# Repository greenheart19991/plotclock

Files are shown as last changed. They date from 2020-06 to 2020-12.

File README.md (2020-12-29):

# Plotclock

A robotic clock that writes current time with a marker.  

The way it functions is simple: the robot draws the time
on every new minute. At the beginning of a minute previously
drawn time becomes erased and new one appears on the board
again.

<p align="center">
  
</p>

## Demo

<p align="center">
  
</p>

## Table of Contents

* [Prerequisites](#prerequisites)
    - [Software](#software)
    - [Hardware & Supplies](#hardware--supplies)
* [Getting Components Ready](#getting-components-ready)
* [Assembling](#assembling)
    - [Mechanics](#mechanics)
    - [Electronics](#electronics)
        + [Prepare RTC Module](#prepare-rtc-module)
        + [Setup Voltage Regulator](#setup-voltage-regulator)
        + [Wiring Diagram](#wiring-diagram)
    - [Assembled Project](#assembled-project)
* [Firmware](#firmware)
    - [Installation](#installation)
    - [Calibration](#calibration)
* [Operating Details](#operating-details)
    - [Positioning To Specific Point](#positioning-to-specific-point)
    - [Drawing Chars](#drawing-chars)
    - [Boundaries](#boundaries)
* [Customization](#customization)
* [Known Issues](#known-issues)
* [Acknowledgments](#acknowledgments)

## Prerequisites

### Software

* Arduino IDE;
* KOMPAS-3D v18 in case you want to customize components.

### Hardware & Supplies

* Arduino UNO (any Rev);
* SG90 servo motors - x3;
* LM2596S step-down voltage regulator;
* ChronoDot V2.0 real time clock module;
* 4.7k Ohm resistors - x2 (for ChronoDot module);
* CR2016 battery;
* 5.5 x 2.1mm DC Female to 2 Male power splitter cable;
* 5.5 x 2.1mm power jack socket;
* DC power supply 12V 2A;
* Whiteboard marker (dry-wipe);

##### Screws & Nuts

* M3 x 12mm pan head screws - x8; 
* M3 x 16mm pan head screws - x1;
* M2.5 x 16mm pan head screws - x7; 
* M3 nuts - x9;
* M2.5 nuts - x7;
* M3 washers - x7;
* M2.5 washers - x1;
* SG90 default screws;

##### Other

* Jumper wires;
* Some glue;
* Some screws and nuts to fix the circuits.

## Getting Components Ready

It is designed to print all of the robot components with 3d-printer.
But you are free to choose another way to produce them.

You can find 3d-models of components under **plotclock_details**
directory. There are both separate files for each component
and **all_in_one** file that contains all of them.
Both are exported to STL format and ready to print.

## Assembling

### Mechanics

Put components together according to pictures below.

<p align="center">
  
</p>

<p align="center">
  
</p>

<p align="center">
  
</p>

Before joining default servo levers to servos themselves
(on the pictures above they have already been joined), set
servo shafts in corresponding positions:
* servo bottom: all the way to the end of min angle;
* servo right: all the way to the end of min angle;
* servo left: all the way to the end of max angle.  

Next, without rotating shafts, attach servo levers to servos
exactly as on the pictures below. After that you can rotate servo
shafts as you want and join printed levers.

<p align="center">
  
</p>

<p align="center">
  
</p>

When joining levers using screws and nuts, glue nuts to
levers to prevent them from loosening.

<p align="center">
  
</p>

<p align="center">
  
</p>

<p align="center">
  
</p>

<p align="center">
  
</p>

<p align="center">
  
</p>

<p align="center">
  
</p>

<p align="center">
  
</p>

Glue a piece of either cloth or cotton to eraser.

<p align="center">
  
</p>

<p align="center">
  
</p>

### Electronics

#### Prepare RTC Module

1. Solder both of pin headers into ChronoDot v2.0 RTC module.
1. Solder both of resistors into the module.
1. Install CR2016 battery on the module.

<p align="center">
  
</p>

#### Setup Voltage Regulator

Put 12V into the LM2596S voltage regulator and adjust it down
to make an output voltage 5.5V.  

#### Wiring Diagram

Connect all the modules together according to the wiring diagram
below.

<p align="center">
  
</p>

To prevent PCBs from moving make something kind of platform or
box for them and fix PCBs on it with screws and nuts.

### Assembled Project

<p align="center">
  
</p>

## Firmware

Sketch and its dependencies are located under **plotclock_code**
directory.

### Installation

Copy all the libraries from **plotclock_code/libraries** directory
to your machine's Arduino libraries directory. Now you are
ready to compile and upload the sketch.

### Calibration 

To be sure marker is positioned correctly you should calibrate
servo values for some predefined positions. Set appropriate values
for the following macros in the sketch:
* `SERVO_LEFT_ANGLE_180` - left servo value when its lever
rotated 180 degrees and is parallel to the board;
* `SERVO_LEFT_ANGLE_90` - left servo value when its lever
rotated 90 degrees and is perpendicular to the board;
* `SERVO_RIGHT_ANGLE_0` - right servo value when its lever
rotated 0 degrees and is parallel to the board.

This lever positions are shown in pictures below.

<p align="center">
  
</p>

<p align="center">
  
</p>

To calibrate Z-axis marker positioning, change the following
macros of bottom servo values:
* `SERVO_BOTTOM_PV_WR_BOTTOM` - position of marker when it touches
the board and chars becomes written;
* `SERVO_BOTTOM_PV_WR_UP` - position of marker to move it between
chars without writing a line;
* `SERVO_BOTTOM_PV_ERS_BOTTOM` - marker is in the eraser;
* `SERVO_BOTTOM_PV_FULLUP` - marker is above the eraser. 

After calibrating and uploading the sketch the robot can be
considered fully assembled and good to go. Since RTC module contains
the battery you don't have to reupload the sketch whenever
you turn the power off to setup the actual time - the module
keeps track of it by itself.

## Operating Details

This section describes provided solution for drawing figures
and intended to help you to deal with sketch and customize
it if necessary.

### Positioning To Specific Point

To move marker to specific point of the drawing plane
you have to rotate servo shafts by specific angle.
In order to draw a char you have to perform a series
of movements to different points; for each of them
you have to know rotation angles for both servo left
and right shafts.

To provide an ability to move the marker by specifying
position of point but not the rotation angles,
virtual coordinate plane was defined. The origin of the
plane is located relative to the servo shafts axes,
and it's position is configurable.

Plane lines unit is millimeter. It thus allows you to
understand the physical location of particular point
without additional units conversion.

This coordinate plane is shown on picture below.
Blue, red and green colors indicate the corresponding
parts of the 'arms' lever system (top view) for one
of the possible marker positions. Point D here is a marker
position, and points A and B indicate servo shafts axes.
The AK distance is equal to the length of the AF lever.
Distances OL and LN are customizable and added to provide
ability to configure origin position.

<p align="center">
  
</p>

Since all of the valuable distances between points are known
and distances MD and DN can be calculated from provided x and y
coordinates, it is possible to calculate the angles FAB and ABG
that represent either angles of the servos or those from which
they can be obtained (servo left angle = FAB, servo right
angle = 180 - ABG).

Algorithm to find these values is implemented in `getServoAngles`
function. To move the marker use `moveTo` function. It uses
`getServoAngles` within itself.

### Drawing Chars

Since coordinate plane is defined, you can describe any figure
you want with a function. And, as soon as you define a
function, you can draw this figure by iterating over axis values,
passing these values to a function and thus getting the coordinates
of points that outline of figure consists of.

Exactly this way all chars becomes drawn. But, in order to simplify
functions, chars are described as a set of primitives.
These are lines, circles and ellipses.

For example, number '1' consists of 2 lines, while number '8' is
2 ellipses. Hence, to draw these numbers the robot sequentially
draw their primitives.

### Boundaries

Due to design features, not all of the board surface area is available
for drawing. For current design all the points that the robot can
positions is shown on picture below.

This area is indicated in red. The board is located according
to its actual location. Black rectangle indicates the max area
determined for drawing chars.

<p align="center">
  
</p>

Take this information into account if you want to customize
chars, positions or sizes, or if you going to draw your own figures.

## Customization

You can find editable models of the robot components under
**plotclock_details/kompas_models** directory. 

The project also provides a tool to show available drawing
area (described above) for a specific design setup. This
tool is located under **plotclock_design** directory and
can help you determine sizes or positions of different
components for new design and define drawing area boundaries.

## Known Issues

SG90 are pretty chip servos and cannot provide guaranteed
ability to rotate their shaft by an angle lower then
~0.75 degree under the marker weight. Therefore quite big
positioning errors occur. As a result there are jagged lines
and currently no ability of physically accurate positioning.

To solve it, more accurate and expensive servos should be
used to give an ability to rotate shafts by at least 0.1 degree.

## Acknowledgments

Thanks to [joo](https://www.thingiverse.com/joo/about)
from [Thingiverse](https://www.thingiverse.com/) for idea
and initial design of components. See original project
[here](https://www.thingiverse.com/thing:248009#Instructions).

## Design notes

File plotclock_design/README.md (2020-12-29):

# Plotclock Design

A tool to show available drawing area for a specific design setup
of the Plotclock.

It can be useful in case you are customizing existing components
or creating your own design. It can help you determine sizes of
these components as well as their positions and drawing area
boundaries.

## Usage

To start the tool open index.html in browser. You'll see
all the points to that marker can be positioned for currently
set robot design.

To edit components settings, edit corresponding constants in
*plotclock.js* file and refresh the page to update the area.

In case available drawing area for some reason was not be rendered
check your design setup and see occurred errors in browser console.

### Component Settings

All the constants are named according to points and segments
described in 'Operating Details' section of main README.
Take a look on the figure provided in this section to determine
constant components.

### Display Settings

You can also change some display behaviour. Main setting here
is `pxInUn` that specifies number of display pixels per
coordinate plane unit. The larger value you set, the larger image
will be, and the higher resolution you will have. You can find this
setting under `show points on page` section in code. 

### Overlay Components 

The tool also provides a Photoshop mockup that can simplify
you putting the board outline and eraser on created image
and determining the chars drawing area. You can find this
mockup as well as example result of tool usage
(for current design setup) under **coverage_maps** directory. 

## Known Issues

Due to representation of numbers in computer, calculation
errors take place. Thus for some **correct** design settings
an error can be thrown and coverage map will not be rendered.
In such situation in console you'll see an error like this:

<p align="center">
  
</p>

Currently, to work around this issue you should change
your design settings a little bit, e.g. for one tenth of mm.

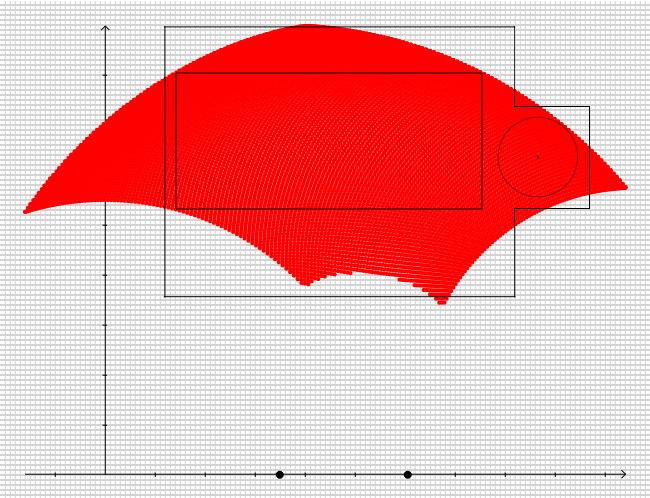
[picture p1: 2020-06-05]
plotclock_design/coverage_maps/coverage_map_x1.png

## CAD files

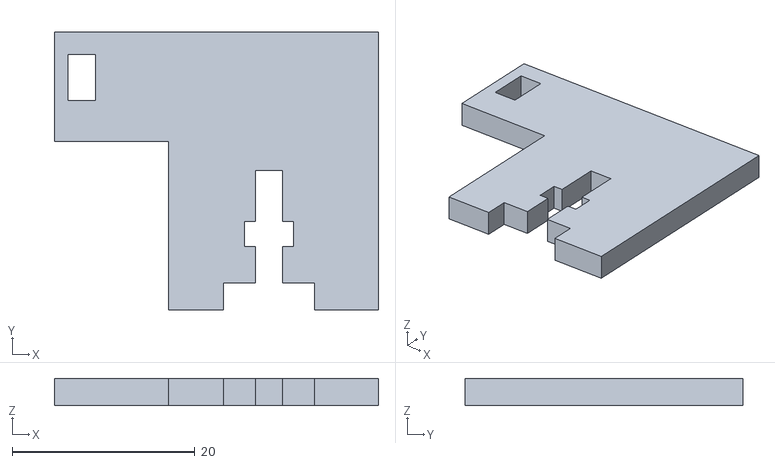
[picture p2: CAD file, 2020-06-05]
plotclock_details/component_8.stl
35.5 x 30.5 x 3.00

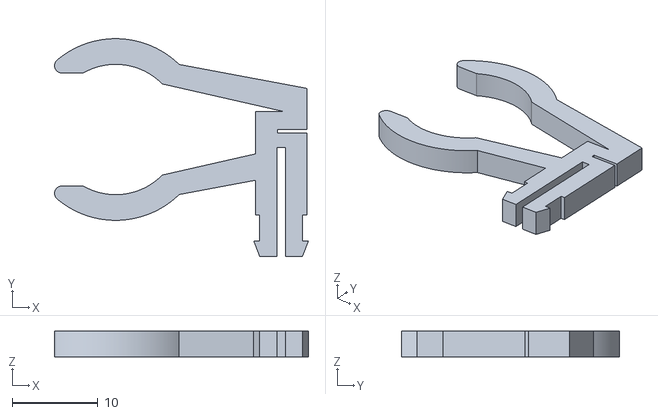
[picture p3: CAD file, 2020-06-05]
plotclock_details/component_11.stl
29.6 x 25.4 x 3.00

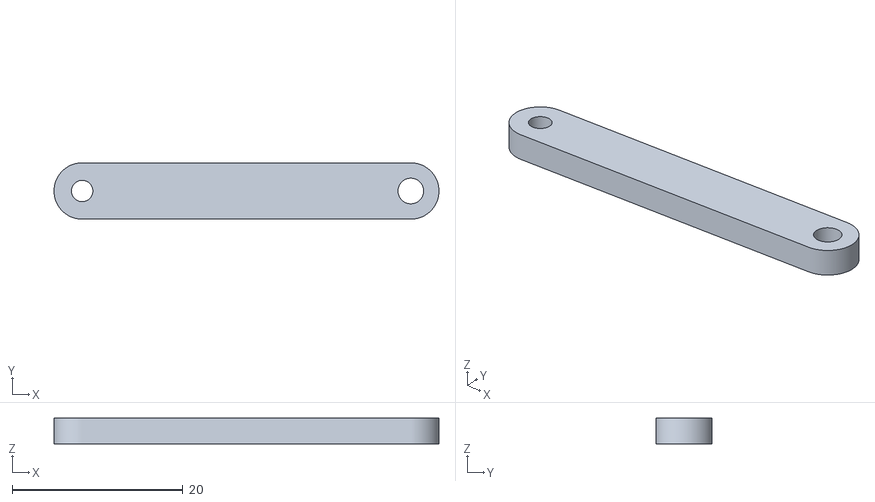
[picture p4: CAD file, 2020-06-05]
plotclock_details/component_4.stl
45.1 x 6.60 x 3.00

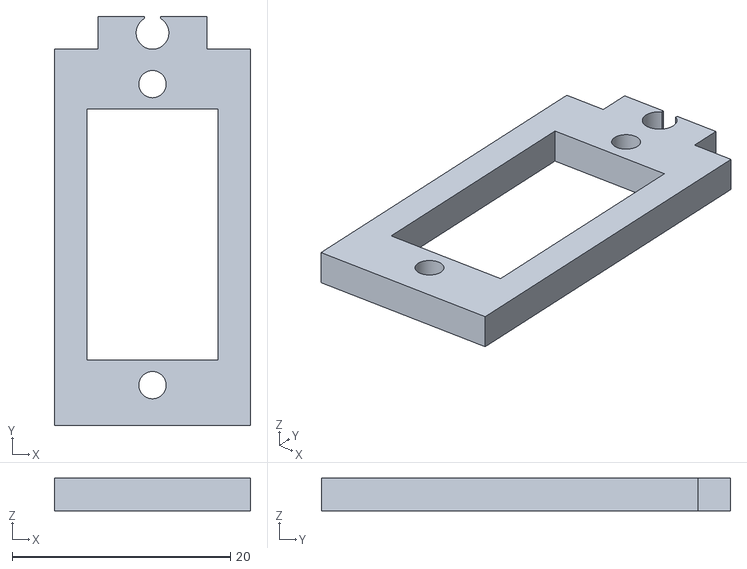
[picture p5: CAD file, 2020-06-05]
plotclock_details/component_10.stl
18.0 x 37.5 x 3.00

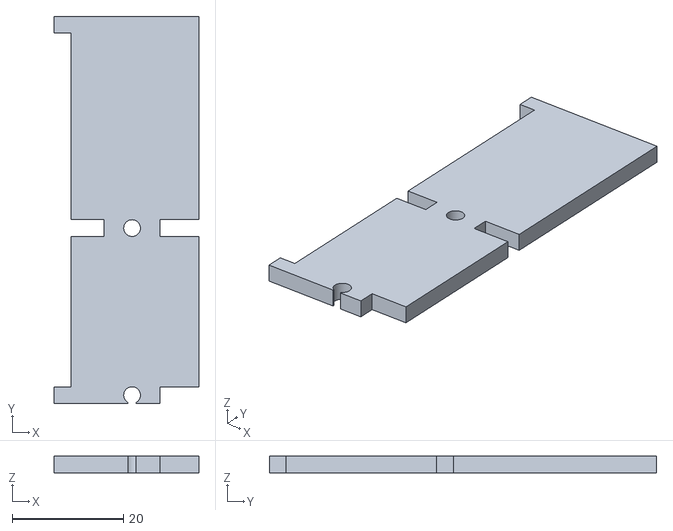
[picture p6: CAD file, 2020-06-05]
plotclock_details/component_6.stl
26.0 x 69.5 x 3.00

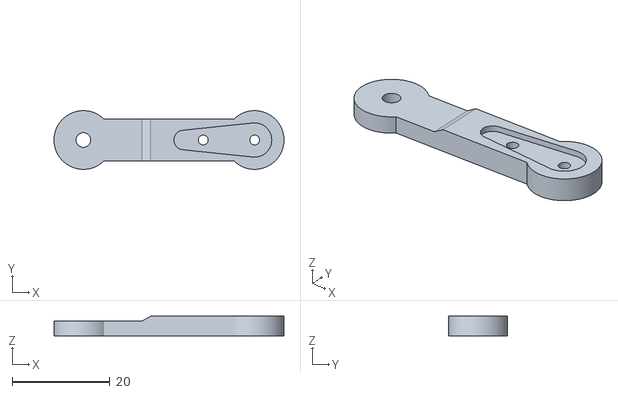
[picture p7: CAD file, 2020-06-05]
plotclock_details/component_1.stl
47.0 x 12.0 x 4.00

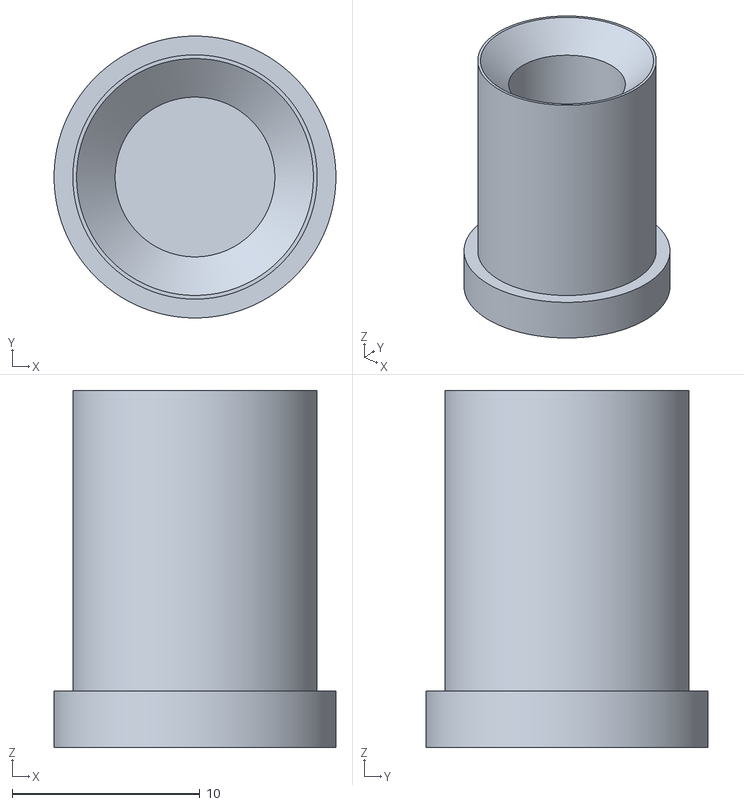
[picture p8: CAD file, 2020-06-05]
plotclock_details/eraser.stl
15.0 x 15.0 x 19.0

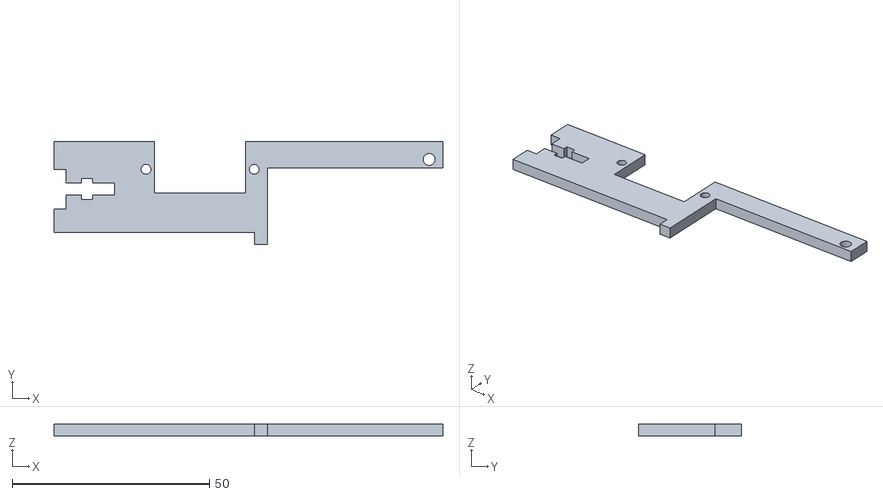
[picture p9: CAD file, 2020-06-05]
plotclock_details/component_3.stl
98.5 x 26.0 x 3.00

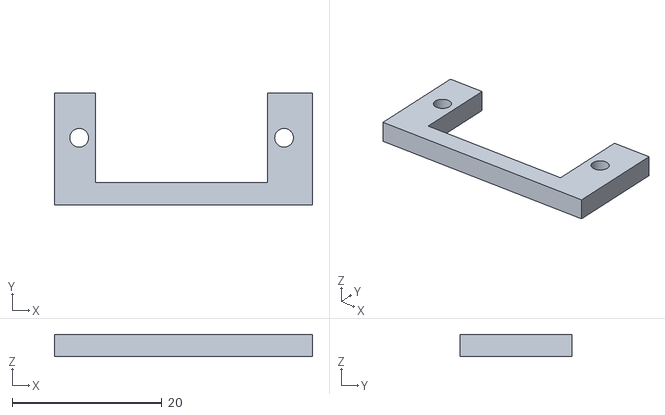
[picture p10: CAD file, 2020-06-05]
plotclock_details/component_12.stl
34.5 x 15.0 x 3.00

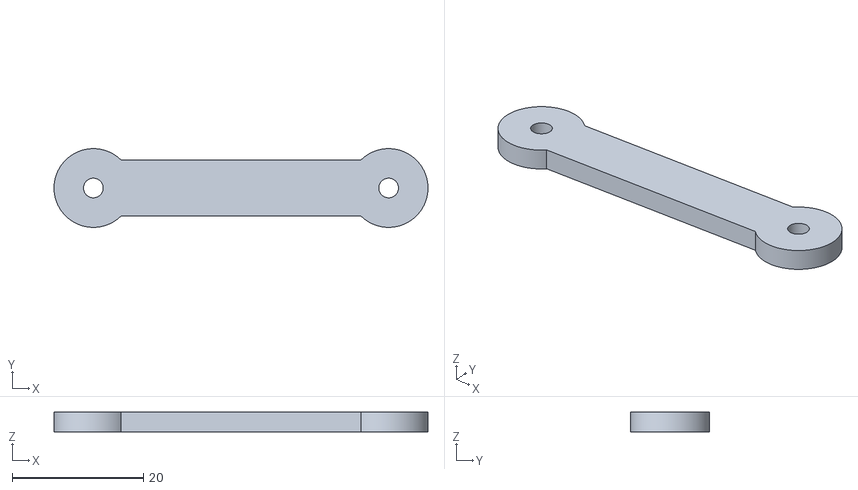
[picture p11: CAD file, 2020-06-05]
plotclock_details/component_15.stl
57.0 x 12.0 x 3.00

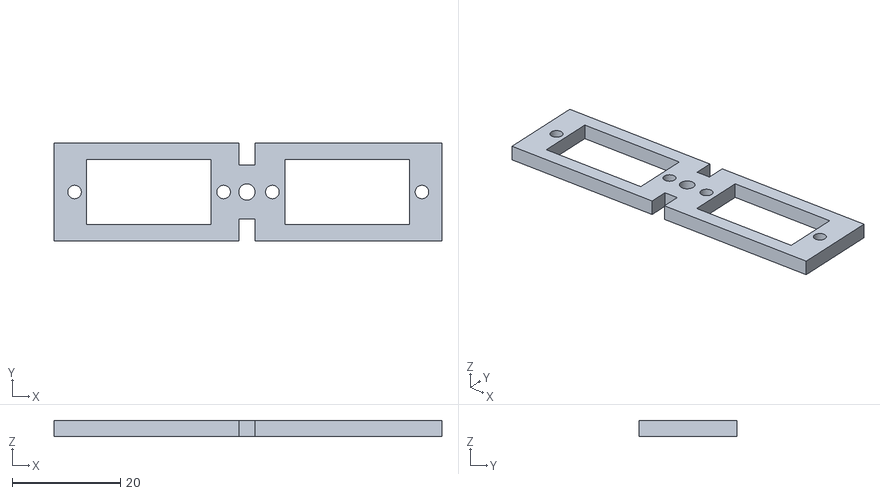
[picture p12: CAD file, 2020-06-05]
plotclock_details/component_9.stl
71.6 x 18.0 x 3.00

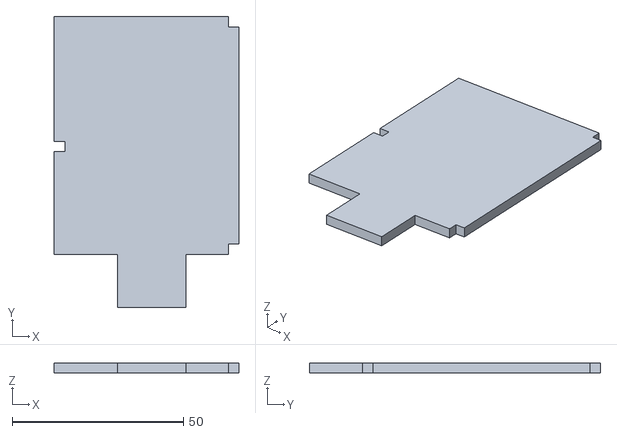
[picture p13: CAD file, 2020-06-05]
plotclock_details/component_5.stl
54.0 x 85.0 x 3.00

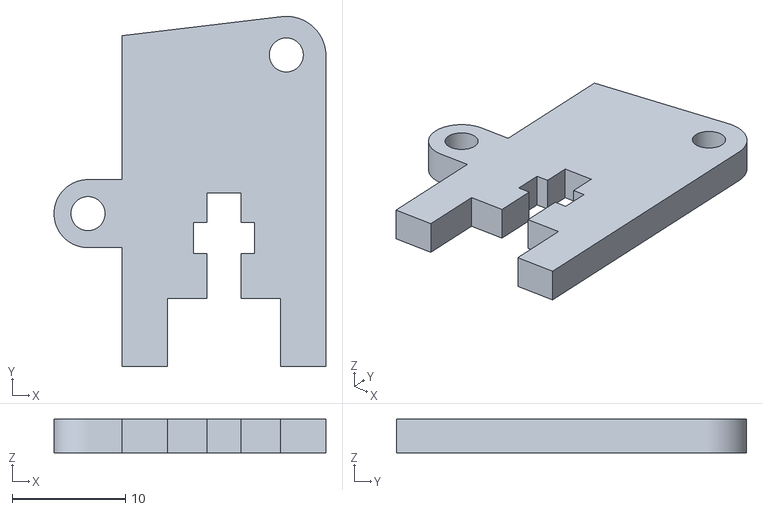
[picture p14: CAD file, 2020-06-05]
plotclock_details/component_13.stl
24.0 x 30.9 x 3.00

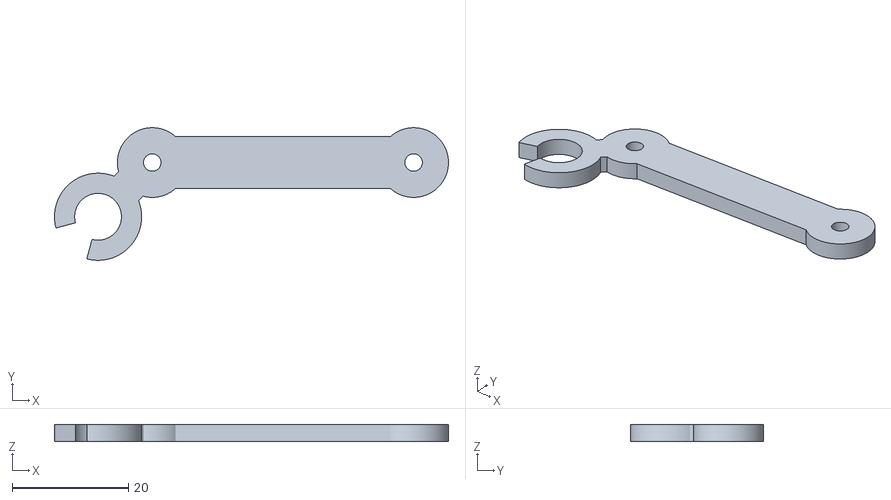
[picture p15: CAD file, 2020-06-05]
plotclock_details/component_14.stl
67.8 x 22.8 x 3.00

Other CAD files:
plotclock_details/component_7.stl

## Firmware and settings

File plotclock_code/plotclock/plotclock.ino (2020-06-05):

#include <EEPROM.h>
#include <Servo.h>
#include "RTClib.h"
#include "utils.h"

// note:
// 1) measurement of widths, distances, offsets, area boundaries etc.
//    set in coordinate plane units (mm in this case);
// 2) angles set in degrees.

// drawing area boundaries
// (where the time is drawing in)
#define DA_MIN_X 19
#define DA_MIN_Y 61.2
#define DA_MAX_X 71.2
#define DA_MAX_Y 77.2

// eraser position
#define ERS_X 87
#define ERS_Y 66

// punctuation mark width relative to char width
#define PM_REL_WIDTH 0.65

// offsets
#define LK 0 // any value
#define OL 0 // >= 0

// design settings
#define AB 25.6
#define AF 35
#define BG 35
#define FC 45.1
#define CG 45.1
#define CD 13.2

// from 0 to 180 deg
#define DCF 135

// bounding angles
#define MAX_FCG 150
#define MAX_CFA 170
#define MAX_CGB 170

// servos min and max control values
#define SERVO_MIN 500
#define SERVO_MAX 2400

// servos calibrated positions
#define SERVO_LEFT_ANGLE_180 2220
#define SERVO_LEFT_ANGLE_90 1250
#define SERVO_RIGHT_ANGLE_0 750

// bottom servo values for predefined positions
#define SERVO_BOTTOM_PV_WR_BOTTOM 1479
#define SERVO_BOTTOM_PV_WR_UP 1380
#define SERVO_BOTTOM_PV_ERS_BOTTOM 1395
#define SERVO_BOTTOM_PV_FULLUP 1120

// servos move settings

// controlled (smooth) move settings

// control values step for left and right servos while iterating from A to B position,
// in servo control values (microseconds)
#define SERVO_LR_SPEED_CON_STEP 1
// delay after each iteration,
// in microseconds
#define SERVO_LR_SPEED_CON_DELAY 600

// uncontrolled move settings

// delay after writing control values to servos to give them time to move shafts,
// in milliseconds
#define SERVO_LR_SPEED_UNCON_DELAY 300

#define SERVO_BOTTOM_SPEED_CON_STEP 1
#define SERVO_BOTTOM_SPEED_CON_DELAY 1620
#define SERVO_BOTTOM_SPEED_UNCON_DELAY 500

// axis values iteration steps,
// in coordinate plane units
#define CALC_DRAWING_STEP 0.336
#define CALC_CLEARING_STEP 1.8

// rtc & date saving settings
#define EEPROM_ADDR_PREV_COMP_DT 0
#define NO_ALARM_INT 0

// pins
#define PIN_ALARM_INT 2
#define PIN_SERVO_LEFT 9
#define PIN_SERVO_RIGHT 10
#define PIN_SERVO_BOTTOM 11

typedef enum lift_stage {
  LIFT_WR_BOTTOM,
  LIFT_WR_UP,
  LIFT_ERS_BOTTOM,
  LIFT_FULLUP
};

typedef struct servo_angles {
  float left;
  float right;
};

// char width,
// 4 means there is 4 chars
const float CHAR_WIDTH = ((float)DA_MAX_X - DA_MIN_X) / (4 + PM_REL_WIDTH);
// punctuation mark width
const float PM_WIDTH = CHAR_WIDTH * PM_REL_WIDTH;

// calculated constants

const float DA_HEIGHT = (float)DA_MAX_Y - DA_MIN_Y;
const float DA_MIDDLE_Y = DA_MIN_Y + DA_HEIGHT / 2;

const float servoMicrosecondsPerAngle =
  (float)(SERVO_LEFT_ANGLE_180 - SERVO_LEFT_ANGLE_90) / 90;

const float FD = getSideBy2SidesAndAngle(CD, FC, DCF);
const float LA = (float)LK + AF;
const float DFC = getAngleBy3Sides(FD, FC, CD);

// program variables

float charAreaStartX = (float)DA_MIN_X;

Servo servoLeft;
Servo servoRight;
Servo servoBottom;

short servoLeftLastMicroseconds;
short servoRightLastMicroseconds;
short servoBottomLastMicroseconds;

RTC_DS3231 rtc;
bool isAlarm = false;
bool isInitialDrawing = true;

// calculate angles of left and right servos for specified marker position
servo_angles* getServoAngles(const float x, const float y) {
  const float DN = y - OL;
  
  if (DN < 0) {
    return nullptr;
  }

  const float NA = abs(LA - x);
  const float AD = sqrt(sq(DN) + sq(NA));
  const float NAD = degrees(atan(DN / NA));

  if (!doesTriangleExist(FD, AF, AD)) {
    return nullptr;
  }
  
  const float DFA = getAngleBy3Sides(FD, AF, AD);
  const float CFA = DFA - DFC;

  if (!doesTriangleAngleExist(CFA) || CFA > MAX_CFA) {
    return nullptr;
  }

  const float CA = getSideBy2SidesAndAngle(FC, AF, CFA);
  const float FAC = getAngleBy3Sides(AF, CA, FC);
  const float FCA = 180 - CFA - FAC;

  const float DAC = getAngleBy3Sides(AD, CA, CD);
  const float FAD = (DCF + FCA <= 180)
    ? FAC - DAC
    : FAC + DAC;

  const float FAB = (x < LA)
    ? FAD + (180 - NAD)
    : FAD + NAD;

  if (FAB > 180) {
    return nullptr;
  }

  const float CAB = FAB - FAC;
  const float CB = getSideBy2SidesAndAngle(CA, AB, CAB);
  
  const float ABC = getAngleBy3Sides(AB, CB, CA);

  if (!doesTriangleExist(CB, BG, CG)) {
    return nullptr;
  }

  const float CBG = getAngleBy3Sides(CB, BG, CG);
  const float CGB = getAngleBy3Sides(CG, BG, CB);
  if (CGB > MAX_CGB) {
    return nullptr;
  }

  const float ABG = ABC + CBG;
  if (ABG > 180) {
    return nullptr;
  }

  const float ACB = 180 - CAB - ABC;
  const float BCG = 180 - CBG - CGB;
  const float FCG = FCA + ACB + BCG;

  if (FCG > MAX_FCG) {
    return nullptr;
  }

  // servo left angle = FAB
  // servo right angle = 180 - ABG

  return new servo_angles {
    FAB,
    180 - ABG
  };
}

void moveTo(const float x, const float y, const bool controlSpeed = true, const bool waitMoving = true) {
  const servo_angles* angles = getServoAngles(x, y);
  if (angles == nullptr) {
    return;
  }

  // calculate and move from predefined
  // calibrated positions
  const float servoLeftAngleFrom180 = 180 - angles->left;
  const float servoRightAngleFrom0 = angles->right;

  // + 0.5 - round instead of floor
  const short servoLeftMicrosecondsFrom180 =
    (int)(servoLeftAngleFrom180 * servoMicrosecondsPerAngle + 0.5);
    
  const short servoRightMicrosecondsFrom0 =
    (int)(servoRightAngleFrom0 * servoMicrosecondsPerAngle + 0.5);

  const short servoLeftMicroseconds = SERVO_LEFT_ANGLE_180 - servoLeftMicrosecondsFrom180;
  const short servoRightMicroseconds = SERVO_RIGHT_ANGLE_0 + servoRightMicrosecondsFrom0;

  if (controlSpeed) {
    const int8_t servoLeftDirCoef = servoLeftMicroseconds > servoLeftLastMicroseconds ? 1 : -1;
    const int8_t servoRightDirCoef = servoRightMicroseconds > servoRightLastMicroseconds ? 1 : -1;
    
    const short servoLeftDiff = abs(servoLeftMicroseconds - servoLeftLastMicroseconds);
    const short servoRightDiff = abs(servoRightMicroseconds - servoRightLastMicroseconds);
    const short biggerDiff = servoLeftDiff > servoRightDiff ? servoLeftDiff : servoRightDiff;

    const float servoLeftStepCoef = (float)servoLeftDiff / biggerDiff;
    const float servoRightStepCoef = (float)servoRightDiff / biggerDiff;

    float i = 0;
    while (i < biggerDiff) {
      servoLeft.writeMicroseconds(servoLeftLastMicroseconds + (short)(i * servoLeftStepCoef * servoLeftDirCoef));
      servoRight.writeMicroseconds(servoRightLastMicroseconds + (short)(i * servoRightStepCoef * servoRightDirCoef));
      delayMicroseconds(SERVO_LR_SPEED_CON_DELAY);
      
      i += SERVO_LR_SPEED_CON_STEP;
    }
  
    servoLeft.writeMicroseconds(servoLeftMicroseconds);
    servoRight.writeMicroseconds(servoRightMicroseconds);
    delayMicroseconds(SERVO_LR_SPEED_CON_DELAY);
  } else {
    servoLeft.writeMicroseconds(servoLeftMicroseconds);
    servoRight.writeMicroseconds(servoRightMicroseconds);

    if (waitMoving) {
      delay(SERVO_LR_SPEED_UNCON_DELAY);
    }
  }

  delete angles;

  servoLeftLastMicroseconds = servoLeftMicroseconds;
  servoRightLastMicroseconds = servoRightMicroseconds;
}

void lift(const lift_stage stage, const bool controlSpeed = true, const bool waitLifting = true) {
  short microseconds;
  
  switch(stage) {
    case LIFT_WR_BOTTOM:  microseconds = SERVO_BOTTOM_PV_WR_BOTTOM;  break;
    case LIFT_WR_UP:      microseconds = SERVO_BOTTOM_PV_WR_UP;      break;
    case LIFT_ERS_BOTTOM: microseconds = SERVO_BOTTOM_PV_ERS_BOTTOM; break;
    case LIFT_FULLUP:     microseconds = SERVO_BOTTOM_PV_FULLUP;     break;

    default:
      return;
  }

  if (controlSpeed) {
    const int8_t dirCoef = microseconds > servoBottomLastMicroseconds ? 1 : -1;
    const short diff = abs(microseconds - servoBottomLastMicroseconds);
  
    float i = 0;
    while (i < diff) {
      servoBottom.writeMicroseconds(servoBottomLastMicroseconds + (short)i * dirCoef);
      delayMicroseconds(SERVO_BOTTOM_SPEED_CON_DELAY);
      
      i += SERVO_BOTTOM_SPEED_CON_STEP;
    }
  
    servoBottom.writeMicroseconds(microseconds);
    delayMicroseconds(SERVO_BOTTOM_SPEED_CON_DELAY);
  } else {
    servoBottom.writeMicroseconds(microseconds);
    
    if (waitLifting) {
      delay(SERVO_BOTTOM_SPEED_UNCON_DELAY);
    }
  }
  
  servoBottomLastMicroseconds = microseconds;
}

void draw_0() {
  const float a = CHAR_WIDTH * 5 / 11;
  const float b = DA_HEIGHT / 2;

  float elemStartX = charAreaStartX + CHAR_WIDTH / 2 - a;
  float elemStartY = DA_MIDDLE_Y;

  moveTo(elemStartX, elemStartY);
  lift(LIFT_WR_BOTTOM);

  float x;
  float y;

  // x & y - values from ellipse origin
  // bottom half-ellipse
  for (x = -a + CALC_DRAWING_STEP; x <= a; x += CALC_DRAWING_STEP) {
    y = getHalfEllipseAbsY(x, a, b);
    moveTo(elemStartX + (a + x), elemStartY - y);
  }

  // top half-ellipse
  // continue from last position
  for (x -= CALC_DRAWING_STEP; x >= -a; x -= CALC_DRAWING_STEP) {
    y = getHalfEllipseAbsY(x, a, b);
    moveTo(elemStartX + (a + x), elemStartY + y);
  }

  lift(LIFT_WR_UP);
}

void draw_1() {  
  float currentElemStartX = charAreaStartX + CHAR_WIDTH / 3;
  float currentElemStartY = DA_MIN_Y + DA_HEIGHT / 2;
  float currentElemEndX = charAreaStartX + (CHAR_WIDTH - CHAR_WIDTH / 5);
  float currentElemEndY = DA_MAX_Y;
  
  moveTo(currentElemStartX, currentElemStartY);
  lift(LIFT_WR_BOTTOM);

  float x;
  float y;

  for (x = currentElemStartX + CALC_DRAWING_STEP; x <= currentElemEndX; x += CALC_DRAWING_STEP) {
    y = getLineY(x, currentElemStartX, currentElemStartY, currentElemEndX, currentElemEndY);
    moveTo(x, y);
  }

  currentElemStartX = currentElemEndX;
  currentElemStartY = currentElemEndY;
  currentElemEndY = DA_MIN_Y;

  for (y = currentElemStartY; y >= currentElemEndY; y -= CALC_DRAWING_STEP) {
    moveTo(currentElemStartX, y);
  }

  lift(LIFT_WR_UP);
}

void draw_2() {
  const float r = CHAR_WIDTH / 2;

  float currentElemStartX = charAreaStartX;
  float currentElemStartY = DA_MAX_Y - r;
  float currentElemEndX;
  float currentElemEndY;

  moveTo(currentElemStartX, currentElemStartY);
  lift(LIFT_WR_BOTTOM);

  float x;
  float y;

  // x & y - values from circle origin
  // top half-circle
  for (x = -r + CALC_DRAWING_STEP; x <= r; x += CALC_DRAWING_STEP) {
    y = getHalfCircleAbsY(x, r);
    moveTo(currentElemStartX + (r + x), currentElemStartY + y);
  }

  currentElemStartX += 2 * r;
  // currentElemStartY stays the same
  currentElemEndX = charAreaStartX;
  currentElemEndY = DA_MIN_Y;

  for (x = currentElemStartX; x >= currentElemEndX; x -= CALC_DRAWING_STEP) {
    y = getLineY(x, currentElemStartX, currentElemStartY, currentElemEndX, currentElemEndY);
    moveTo(x, y);
  }

  currentElemStartX = currentElemEndX;
  // currentElemStartY = currentElemEndY; but it's
  // not important anymore
  currentElemEndX = charAreaStartX + CHAR_WIDTH;
  // currentElemEndY stays the same

  for (x = currentElemStartX; x <= currentElemEndX; x += CALC_DRAWING_STEP) {
    moveTo(x, currentElemEndY);
  }

  lift(LIFT_WR_UP);
}

void draw_3() {
  const float a = CHAR_WIDTH * 5 / 11;
  const float b = DA_HEIGHT / 4;

  float elemStartX = charAreaStartX + CHAR_WIDTH / 2 - a;
  float elemStartY = DA_MAX_Y - b;

  moveTo(elemStartX, elemStartY);
  lift(LIFT_WR_BOTTOM);

  float x;
  float y;

  // x & y - values from ellipse origin
  // top half-ellipse
  for (x = -a + CALC_DRAWING_STEP; x <= a; x += CALC_DRAWING_STEP) {
    y = getHalfEllipseAbsY(x, a, b);
    moveTo(elemStartX + (a + x), elemStartY + y);
  }

  // right bottom quarter-ellipse
  for (x -= CALC_DRAWING_STEP; x >= 0; x -= CALC_DRAWING_STEP) {
    y = getHalfEllipseAbsY(x, a, b);
    moveTo(elemStartX + (a + x), elemStartY - y);
  }

  elemStartY -= 2 * b;

  // right top quarter-ellipse
  for (x += CALC_DRAWING_STEP; x <= a; x += CALC_DRAWING_STEP) {
    y = getHalfEllipseAbsY(x, a, b);
    moveTo(elemStartX + (a + x), elemStartY + y);
  }

  // bottom half-ellipse
  for (x -= CALC_DRAWING_STEP; x >= -a; x -= CALC_DRAWING_STEP) {
    y = getHalfEllipseAbsY(x, a, b);
    moveTo(elemStartX + (a + x), elemStartY - y);
  }

  lift(LIFT_WR_UP);
}

void draw_4() {
  float currentElemStartX = charAreaStartX + CHAR_WIDTH * 4 / 5;
  float currentElemStartY = DA_MIN_Y;
  float currentElemEndY = DA_MAX_Y;
  float currentElemEndX;

  moveTo(currentElemStartX, currentElemStartY);
  lift(LIFT_WR_BOTTOM);

  float x;
  float y;

  for (y = currentElemStartY + CALC_DRAWING_STEP; y <= currentElemEndY; y += CALC_DRAWING_STEP) {
    moveTo(currentElemStartX, y);
  }

  // currentElemStartX stays the same
  currentElemStartY = currentElemEndY;
  currentElemEndX = charAreaStartX;
  currentElemEndY = DA_MIN_Y + CHAR_WIDTH * 2 / 5;

  for (x = currentElemStartX; x >= currentElemEndX; x -= CALC_DRAWING_STEP) {
    y = getLineY(x, currentElemStartX, currentElemStartY, currentElemEndX, currentElemEndY);
    moveTo(x, y);
  }

  currentElemStartX = currentElemEndX;
  currentElemEndX = charAreaStartX + CHAR_WIDTH;
  currentElemStartY = currentElemEndY;

  for (x = currentElemStartX; x <= currentElemEndX; x += CALC_DRAWING_STEP) {
    moveTo(x, currentElemStartY);
  }

  lift(LIFT_WR_UP);
}

void draw_5() {
  const float r = CHAR_WIDTH * 2 / 5;
  
  float currentElemStartX = charAreaStartX + CHAR_WIDTH;
  float currentElemStartY = DA_MAX_Y;
  float currentElemEndX = charAreaStartX + CHAR_WIDTH / 3;
  float currentElemEndY;

  moveTo(currentElemStartX, currentElemStartY);
  lift(LIFT_WR_BOTTOM);

  float x;
  float y;

  for (x = currentElemStartX - CALC_DRAWING_STEP; x >= currentElemEndX; x -= CALC_DRAWING_STEP) {
    moveTo(x, currentElemStartY);
  }

  currentElemStartX = currentElemEndX;
  currentElemEndY = DA_MIN_Y + 2 * r;

  for (y = currentElemStartY; y >= currentElemEndY; y -= CALC_DRAWING_STEP) {
    moveTo(currentElemStartX, y);
  }

  currentElemEndX = charAreaStartX + CHAR_WIDTH - r;
  currentElemStartY = currentElemEndY;

  for (x = currentElemStartX; x <= currentElemEndX; x += CALC_DRAWING_STEP) {
    moveTo(x, currentElemStartY);
  }

  currentElemStartX = currentElemEndX;
  currentElemStartY = DA_MIN_Y + r;
  // currentElemEndX & currentElemEndY are not important anymore

  // x & y - values from circle origin
  // right top quarter-circle
  for (x = 0; x <= r; x += CALC_DRAWING_STEP) {
    y = getHalfCircleAbsY(x, r);
    moveTo(currentElemStartX + x, currentElemStartY + y);
  }

  // bottom half-circle
  for (x -= CALC_DRAWING_STEP; x >= -r; x -= CALC_DRAWING_STEP) {
    y = getHalfCircleAbsY(x, r);
    moveTo(currentElemStartX + x, currentElemStartY - y);
  }

  lift(LIFT_WR_UP);
}

void draw_6() {
  const float r = CHAR_WIDTH * 2 / 5;
  
  float currentElemStartX = charAreaStartX + CHAR_WIDTH / 2;
  float currentElemStartY = DA_MAX_Y;
  float currentElemEndX = currentElemStartX - r;
  float currentElemEndY = DA_MIN_Y + r;

  moveTo(currentElemStartX, currentElemStartY);
  lift(LIFT_WR_BOTTOM);

  float x;
  float y;

  for (x = currentElemStartX; x >= currentElemEndX; x -= CALC_DRAWING_STEP) {
    y = getLineY(x, currentElemStartX, currentElemStartY, currentElemEndX, currentElemEndY);
    moveTo(x, y);
  }

  currentElemStartX = currentElemEndX;
  currentElemStartY = currentElemEndY;
  // currentElemEndX & currentElemEndY are not important anymore

  // x & y - values from circle origin
  // bottom half-circle
  for (x = -r; x <= r; x += CALC_DRAWING_STEP) {
    y = getHalfCircleAbsY(x, r);
    moveTo(currentElemStartX + (r + x), currentElemStartY - y);
  }

  // top half-circle
  for (x -= CALC_DRAWING_STEP; x >= -r; x -= CALC_DRAWING_STEP) {
    y = getHalfCircleAbsY(x, r);
    moveTo(currentElemStartX + (r + x), currentElemStartY + y);
  }

  lift(LIFT_WR_UP);
}

void draw_7() {
  float currentElemStartX = charAreaStartX;
  float currentElemStartY = DA_MAX_Y;
  float currentElemEndX = charAreaStartX + CHAR_WIDTH;
  float currentElemEndY;

  moveTo(currentElemStartX, currentElemStartY);
  lift(LIFT_WR_BOTTOM);

  float x;
  float y;

  for (x = currentElemStartX + CALC_DRAWING_STEP; x <= currentElemEndX; x += CALC_DRAWING_STEP) {
    moveTo(x, currentElemStartY);
  }

  currentElemStartX = currentElemEndX;
  // currentElemStartY stays the same
  currentElemEndX = charAreaStartX + CHAR_WIDTH / 2;
  currentElemEndY = DA_MIN_Y;

  for (x = currentElemStartX; x >= currentElemEndX; x -= CALC_DRAWING_STEP) {
    y = getLineY(x, currentElemStartX, currentElemStartY, currentElemEndX, currentElemEndY);
    moveTo(x, y);
  }

  lift(LIFT_WR_UP);
}

void draw_8() {
  const float a = CHAR_WIDTH * 5 / 11;
  const float b = DA_HEIGHT / 4;

  float elemStartX = charAreaStartX + CHAR_WIDTH / 2 - a;
  float elemStartY = DA_MAX_Y - b;

  moveTo(elemStartX, elemStartY);
  lift(LIFT_WR_BOTTOM);

  float x;
  float y;

  // x & y - values from ellipse origin
  // top half-ellipse
  for (x = -a + CALC_DRAWING_STEP; x <= a; x += CALC_DRAWING_STEP) {
    y = getHalfEllipseAbsY(x, a, b);
    moveTo(elemStartX + (a + x), elemStartY + y);
  }

  // right bottom quarter-ellipse
  for (x -= CALC_DRAWING_STEP; x >= 0; x -= CALC_DRAWING_STEP) {
    y = getHalfEllipseAbsY(x, a, b);
    moveTo(elemStartX + (a + x), elemStartY - y);
  }

  elemStartY -= 2 * b;

  // left top quater-ellipse
  for (; x >= -a; x -= CALC_DRAWING_STEP) {
    y = getHalfEllipseAbsY(x, a, b);
    moveTo(elemStartX + (a + x), elemStartY + y);
  }

  // bottom half-ellipse
  for (x += CALC_DRAWING_STEP; x <= a; x += CALC_DRAWING_STEP) {
    y = getHalfEllipseAbsY(x, a, b);
    moveTo(elemStartX + (a + x), elemStartY - y);
  }

  // right top quater-ellipse
  for (x -= CALC_DRAWING_STEP; x >= 0; x -= CALC_DRAWING_STEP) {
    y = getHalfEllipseAbsY(x, a, b);
    moveTo(elemStartX + (a + x), elemStartY + y);
  }

  elemStartY += 2 * b;

  // left bottom quater-ellipse
  for (; x >= -a; x -= CALC_DRAWING_STEP) {
    y = getHalfEllipseAbsY(x, a, b);
    moveTo(elemStartX + (a + x), elemStartY - y);
  }

  lift(LIFT_WR_UP);
}

void draw_9() {
  const float r = CHAR_WIDTH * 2 / 5;
  
  float currentElemStartX = charAreaStartX + CHAR_WIDTH / 2;
  float currentElemStartY = DA_MIN_Y;
  float currentElemEndX = currentElemStartX + r;
  float currentElemEndY = DA_MAX_Y - r;

  moveTo(currentElemStartX, currentElemStartY);
  lift(LIFT_WR_BOTTOM);

  float x;
  float y;

  for (x = currentElemStartX; x >= currentElemEndX; x -= CALC_DRAWING_STEP) {
    y = getLineY(x, currentElemStartX, currentElemStartY, currentElemEndX, currentElemEndY);
    moveTo(x, y);
  }

  currentElemStartX = currentElemEndX;
  currentElemStartY = currentElemEndY;
  // currentElemEndX & currentElemEndY are not important anymore

  // x & y - values from circle origin
  // top half-circle
  for (x = r; x >= -r; x -= CALC_DRAWING_STEP) {
    y = getHalfCircleAbsY(x, r);
    moveTo(currentElemStartX - (r - x), currentElemStartY + y);
  }

  // bottom half-circle
  for (x += CALC_DRAWING_STEP; x <= r; x += CALC_DRAWING_STEP) {
    y = getHalfCircleAbsY(x, r);
    moveTo(currentElemStartX - (r - x), currentElemStartY - y);
  }

  lift(LIFT_WR_UP);
}

void draw_colon() {
  const float dotsDistance = DA_HEIGHT / 2;
  const float dotsVerticalIndent = (DA_HEIGHT - dotsDistance) / 2;
  
  float currentDotX = charAreaStartX + PM_WIDTH / 2;
  float currentDotY = DA_MAX_Y - dotsVerticalIndent;

  moveTo(currentDotX, currentDotY);
  lift(LIFT_WR_BOTTOM);
  lift(LIFT_WR_UP);

  currentDotY = DA_MIN_Y + dotsVerticalIndent;

  moveTo(currentDotX, currentDotY);
  lift(LIFT_WR_BOTTOM);
  lift(LIFT_WR_UP);
}

void draw(const char* pString) {  
  while (*pString != '\0') {
    const float charWidth = pString[0] == ':'
      ? PM_WIDTH
      : CHAR_WIDTH;

    // here the calculation error should be taken into account.
    // note: when changing the values of physical parameters,
    // the last char can be lost
    if ((charAreaStartX + charWidth) > DA_MAX_X) {
      return;
    }

    switch (pString[0]) {
      case '0': draw_0();     break;
      case '1': draw_1();     break;
      case '2': draw_2();     break;
      case '3': draw_3();     break;
      case '4': draw_4();     break;
      case '5': draw_5();     break;
      case '6': draw_6();     break;
      case '7': draw_7();     break;
      case '8': draw_8();     break;
      case '9': draw_9();     break;
      case ':': draw_colon(); break;
      
      default:
        break;
    }

    charAreaStartX += charWidth;
    pString++;
  }
}
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
void loop() {
  if (isInitialDrawing || isAlarm) {    
    clearArea();
    
    DateTime dt = rtc.now();

    if (isInitialDrawing && isAlarm) {
      rtc.clearAlarm(2);
      isAlarm = false;
    }
    
    char dtString[5];
    sprintf(dtString, "%02d:%02d", dt.hour(), dt.minute());
  
    lift(LIFT_FULLUP);
    moveTo(charAreaStartX, DA_MIN_Y);
    lift(LIFT_WR_UP);
  
    draw(dtString);
  
    lift(LIFT_FULLUP);
    moveTo(ERS_X, ERS_Y);
    lift(LIFT_ERS_BOTTOM);

    if (isInitialDrawing) {
      isInitialDrawing = false;
    } else if (isAlarm) {
      rtc.clearAlarm(2);
      isAlarm = false;
    }
  }
}

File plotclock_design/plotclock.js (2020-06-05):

// --- helper functions ---

const toDegrees = (rAngle) => {
    return rAngle * (180 / Math.PI);
};

const toRadians = (dAngle) => {
    return dAngle * (Math.PI / 180);
};

// get 3rd side of triangle using 2 sides and angle between them
// note: angle in degrees
const getSideBy2SidesAndAngle = (a, b, dAngle) => {
    if (dAngle < 0 || dAngle > 180) {
        throw new RangeError(
            `Incorrect angle: ${dAngle}.\n` +
            'Angle of triangle must be in range [0, 180]'
        );
    }

    const rAngle = toRadians(dAngle);
    return Math.sqrt(a * a + b * b - 2 * a * b * Math.cos(rAngle));
};

// get angle between 'a' and 'b' sides
// note: angle in degrees
const getAngleBy3Sides = (a, b, c) => {
    if (
        (a + b) < c
        || (a + c) < b
        || (b + c) < a
    ) {
        throw new Error(`Triangle a=${a}, b=${b}, c=${c} doesn't exist`);
    }

    const rAngle = Math.acos((a * a + b * b - c * c) / (2 * a * b));
    return toDegrees(rAngle);
};

// --- offsets ---
// feel free to customize

const LK = 0; // any value
const OL = 0; // >= 0

// --- design settings ---
// feel free to customize
// note: angles in degrees,
// distances in coordinate plane units

const AB = 25.6;
const AF = 35;
const BG = 35;
const FC = 45;
const CG = 45;
const CD = 13.2;
const DCF = 133.5;

// --- boundary values ---
// feel free to customize

const maxFCG = 150;
const maxCFA = 170;
const maxCGB = 170;

// --- calculated constants ---

const FD = getSideBy2SidesAndAngle(CD, FC, DCF);
const LA = LK + AF;

// --- algorithm function ---

// get marker position relative to the origin.
// Result is in format of { x, y }.
const getMarkerPosition = (servo1DAngle, servo2DAngle) => {
    if (
        servo1DAngle < 0 || servo1DAngle > 180
        || servo2DAngle < 0 || servo2DAngle > 180
    ) {
        return null;
    }

    const ABG = 180 - servo2DAngle;
    const AG = getSideBy2SidesAndAngle(AB, BG, ABG);
    const GAB = getAngleBy3Sides(AG, AB, BG);
    const FAG = servo1DAngle - GAB;

    if (FAG < 0) {
        return null;
    }

    const FG = getSideBy2SidesAndAngle(AF, AG, FAG);
    if (FG > (FC + CG) || getAngleBy3Sides(FC, CG, FG) > maxFCG) {
        return null;
    }

    const AFG = getAngleBy3Sides(FG, AF, AG);
    const FB = getSideBy2SidesAndAngle(AF, AB, servo1DAngle);

    if (
        getAngleBy3Sides(FB, AB, AF) > ABG
        || GAB > servo1DAngle
    ) {
        return null;
    }

    const FGB = getAngleBy3Sides(FG, BG, FB);

    const CFG = getAngleBy3Sides(FC, FG, CG);
    const CGF = CFG;
    const CFA = CFG + AFG;
    const CGB = CGF + FGB;

    if (CFA > maxCFA || CGB > maxCGB) {
        return null;
    }

    const CA = getSideBy2SidesAndAngle(FC, AF, CFA);
    const FCA = getAngleBy3Sides(FC, CA, AF);
    const FAC = 180 - (CFA + FCA);

    const leftDCA = DCF + FCA;

    const DCA = leftDCA <= 180
        ? leftDCA
        : 360 - leftDCA;

    const DA = getSideBy2SidesAndAngle(CD, CA, DCA);
    const DAC = getAngleBy3Sides(DA, CA, CD);

    const FAD = leftDCA <= 180
        ? FAC - DAC
        : FAC + DAC;

    const LAF = 180 - servo1DAngle;
    const LAD = LAF + FAD;

    const DN = DA * Math.sin(toRadians(LAD));
    const NA = DA * Math.cos(toRadians(LAD));

    const x = LA - NA;
    const y = DN + OL;

    return { x, y };
};

// get angles of servo1 and servo2 for specified marker position.
// Result is in format of { servo1, servo2 }, in degrees.
const getServoAngles = (x, y) => {
    const DN = y - OL;

    if (DN < 0) {
        return null;
    }

    const NA = Math.abs(LA - x);
    const AD = Math.sqrt(DN * DN + NA * NA);
    const NAD = toDegrees(Math.atan(DN / NA));

    const DFA = getAngleBy3Sides(FD, AF, AD);
    const DFC = getAngleBy3Sides(FD, FC, CD);
    const CFA = DFA - DFC;

    if (CFA > maxCFA) {
        return null;
    }

    const CA = getSideBy2SidesAndAngle(FC, AF, CFA);
    const FAC = getAngleBy3Sides(AF, CA, FC);
    const FCA = 180 - CFA - FAC;

    const DAC = getAngleBy3Sides(AD, CA, CD);
    const FAD = (DCF + FCA <= 180)
        ? FAC - DAC
        : FAC + DAC;

    const FAB = x < LA
        ? FAD + (180 - NAD)
        : FAD + NAD;

    if (FAB > 180) {
        return null;
    }

    const CAB = FAB - FAC;
    const CB = getSideBy2SidesAndAngle(CA, AB, CAB);

    const ABC = getAngleBy3Sides(AB, CB, CA);

    const CBG = getAngleBy3Sides(CB, BG, CG);

    const CGB = getAngleBy3Sides(CG, BG, CB);
    if (CGB > maxCGB) {
        return null;
    }

    const ABG = ABC + CBG;
    if (ABG > 180) {
        return null;
    }

    const ACB = 180 - CAB - ABC;
    const BCG = 180 - CBG - CGB;
    const FCG = FCA + ACB + BCG;

    if (FCG > maxFCG) {
        return null;
    }

    return {
        servo1: FAB,
        servo2: 180 - ABG
    };
};
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
